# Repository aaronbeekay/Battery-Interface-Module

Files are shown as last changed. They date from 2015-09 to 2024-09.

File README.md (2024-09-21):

Battery Interface Module (BIM)
========================

Battery Interface Module is a compact, 24-cell lithium battery cell monitor with an onboard microcontroller and CAN communications.

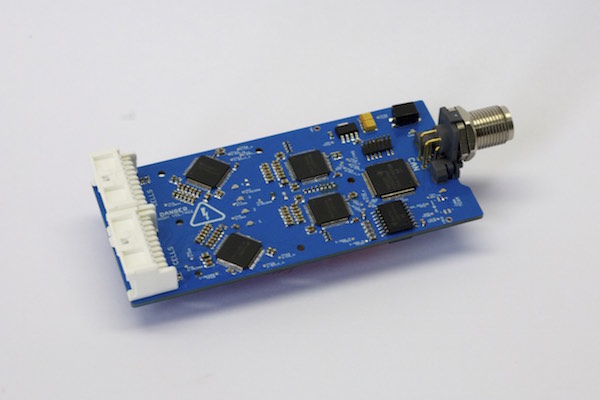
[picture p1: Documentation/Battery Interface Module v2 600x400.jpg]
Image of BIM


*Image: Battery Interface Module v2*

It's built to go on [Buckeye Current](http://current.osu.edu/)'s RW-series electric racing motorcycles. The latest version (v2.0) is designed to integrate with RW-3, a purpose-built racer for the Pikes Peak International Hill Climb.

The Battery Interface Module is built on the TI BQ76PL536A battery-monitor IC. Some features include:

* Voltage monitoring of up to 24 battery cells at precision of ~1 mV
* Thermistor connections for cell temperature monitoring
* Onboard host processor to control battery interface, control balancing, and transmit data over CAN
* Wide input voltage range (4-40 V)
* Isolated interface to battery voltage monitors

You can read more about the Battery Interface Module in the [Battery Interface Module design report]( https://github.com/aaronbeekay/Battery-Interface-Module/raw/main/Documentation/Battery%20Interface%20Module%20report.pdf).

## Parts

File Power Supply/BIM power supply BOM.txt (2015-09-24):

Qty	Description	Mfg Name	Part Num	VID	Vendor Part Num	Parts
4	diode zener 18v 5w axial	ON Semiconductor	1N5355BRLG	DK	1N5355BRLGOSCT-ND	"D1, D2, D3, D4"
1	"2.00mm Pitch MicroClasp? Wire-to-Board Header, Dual Row, Right Angle, 26 Circuits"	Molex	55959-2630	NW	95M2858	X1
2	FUSE BRD MNT 500MA 125VAC 63VDC	Bel Fuse	C1Q 500	DK	507-1075-6-ND	"F1, F2"
20	"Resistor, 1k ohm 63 mW, 1%, 0603"	Multicomp	MC0603WGF1001T5E-TC	NW	58K4448	"R1, R2, R3, R5, R6, R8, R9, R10, R12, R13, R15, R16, R17, R19, R20, R22, R23, R24, R26, R27"
4	"Resistor, 10 ohm, 3W, 5%,"	Multicomp	MOR03SJ0100A19	NW	74M3341	"R7, R14, R21, R28"
4	"CAPACITOR ALUM ELEC, 220UF, 63V, 20%, radial"	Panasonic	ECA-1JM221	NW	96K9194	"C1, C2, C3, C4"
4	*	*	*	*	*	"U$6, U$7, U$8, U$10"
1	"Header, Screw Terminal, 2-pos, 5mm"	TE Connectivity	282836-2	DK	A98076-ND	U$9

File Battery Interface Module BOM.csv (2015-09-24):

Qty | Description | Category | Manufacturer | Manufacturer | Vendor | Vendor part | Cost | Designator
24 | Capacitor, 33 pF, 50V, 5%, NP0, 0402 | Passives | AVX | 04025A330JAT2A | DK | 478-1076-1-ND | 0.02 | C77, C78, C79, C80, C81, C82, C83, C84, C85, C86, C87, C88, C89, C90, C91, C92, C101, C102, C103, C104, C105, C106, C107, C108
1 | DIP switch, 0.05"" pitch, 2pos, 50V | Switches | CTS Electrocomponents | 218-2LPST | DK | CT2182LPST-ND | 1.06 | SW1
1 | M12-5 PCB header, right angle, male pins, shielded | Connectors | Conec | 43-01211 | DK | 626-1513-ND | 10.63 | X4
2 | Micro-Clasp header, 20pos, 2 rows, RA, through-hole | Connectors | Molex | 55959-2030 | NW | 09J7572 | 1.13 | X2, X3
1 | IC, DC/DC Conv, 180MHz, 3.3V-5V in, 3.3V/5V out | ICs | Analog Devices | ADUM5000ARWZ | NW | 19P8235 | 6.99 | IC11
1 | Schottky rectifier, 30V, 1A, SMA | Passives | Diodes Inc | B130-13-F | DK | B130-FDICT-ND | 0.43 | D17
4 | Inductor, Chip, 60ohm, 1.5A, 0603 | Passives | Taiyo Yuden | BKP1608HS600-T | DK | 587-1928-1-ND | 0.047 | L1, L2, L3, L4
4 | IC, Li-Ion battery monitor, LQFP-64 | ICs | Texas Instruments | BQ76PL536APAPT | DK | 296-28926-1-ND | 12.34 | IC1, IC2, IC3, IC4
3 | Capacitor, Ceramic, 470pF 50V, NP0, 0603 | Passives | TDK | C1608C0G1H471J080AA | DK | 445-1289-1-ND | 0.012 | C165, C166, C167
9 | Capacitor, Ceramic, 1UF, 16V, X5R, 10%, 0603 | Passives | TDK | C1608X5R1C105K | NW | 90R7675 | 0.013 | C6, C12, C18, C24, C30, C36, C42, C48, C192
24 | Resistor, 1k ohm, 63 mW, 5%, Thick Film 0402 | CRCW04021K00JNTD | Vishay Dale | CRCW04021K00JNTD | NW | 23C6830 | 0.008 | R10, R11, R12, R47, R48, R49, R50, R51, R52, R53, R54, R55, R56, R57, R58, R59, R60, R61, R62, R63, R64, R65, R66, R67
4 | RES 2.00M OHM 1/16W 1% 0402 SMD | Passives | Vishay Dale | CRCW04022M00FKED | DK | 541-2.00MLCT-ND | 0.005 | R140, R141, R142, R143
12 | Resistor, 1.47k ohm, 100 mW, 0603, 1% | Passives | Vishay Dale | CRCW06031K47FKEA | DK | 541-1.47KHCT-ND | 0.005 | R7, R9, R15, R40, R42, R80, R82, R84, R85, R87, R89, R90
8 | Resistor, 1.82k ohm, 100 mW, 0603, 1% | Passives | Vishay Dale | CRCW06031K82FKEA | DK | 541-1.82KHCT-ND | 0.005 | R6, R8, R39, R41, R81, R83, R86, R88
2 | Resistor, 510k ohm, 100 mW, 1%, Thick Film 0603 | Passives | Vishay Dale | CRCW0603510KFKEA | NW | 52K8595 | 0.005 | R148, R149
1 | Choke, common mode, 100 uH, 500 mA, 25% | Passives | Bourns Inc | DR331-104AE | NW | 29T3649 | 0.32 | L6
25 | Resistor, 1 kohm 100 mW, 1%, Thick Film, 0603 | Passives | Panasonic | ERJ-3EKF1001V | NW | 64R5308 | 0.012 | R1, R2, R3, R4, R5, R13, R14, R16, R17, R18, R20, R21, R22, R23, R24, R26, R27, R28, R29, R30, R32, R33, R34, R35, R36, R135
1 | Resistor, 5.6 kohm, 100 mW, 1%, 0603 | Passives | Panasonic | ERJ-3EKF5601V | NW | 64R5354 | 0.096 | R134
2 | Resistor, 60.4 ohm, 100 mW, 1%, 0603 | Passives | Panasonic | ERJ-3EKF60R4V | NW | 65T8495 | 0.096 | R38, R43
4 | Resistor, 5.5 ohm, 100 mW, 5%, 0603 | Passives | Panasonic | ERJ-3GEYJ5R6V | NW | 65T8659 | 0.002 | R44, R45, R46, R68
2 | Resistor, 82 ohm, 125 mW, 5%, 0805 | Passives | Panasonic | ERJ-6GEYJ820V | NW | 53W4971 | 0.096 | R116, R117
1 | Thermistor, NTC, 10 kohm, 1%, SMD, 0603, b = 3375 K | Passives | Panasonic | ERT-J1VG103FA | NW | 55T6142 | 0.698 | R114
4 | N-channel MOSFET, 25V, 220 mA, SOT-23 | Semiconductors | Fairchild Semiconductor | FDV301N | NW | 58K8856 | 0.034 | Q37, Q39, Q40, Q41
1 | 0.05"" male pin header, 2 rows, 14 positions (TI JTAG) - surface mount, vertical | Connectors | Samtec | FTS-107-01-F-DV | NW | 56P3763 | 0.9 | X6
4 | Capacitor, Ceramic, 10 uF 6.3V, 20%, 0603, X5R | * | Murata | GRM188R60J106ME47D | NW | 24R6334 | 0.12 | C52, C53, C173, C174
18 | Capacitor, Ceramic, 2.2UF, 10%, 25V, 0603, X5R | Passives | Murata | GRM188R61E225KA12D | NW | 13T1193 | 0.107 | C73, C76, C118, C119, C122, C124, C125, C128, C130, C131, C134, C136, C149, C150, C151, C152, C153, C154
57 | Capacitor, Ceramic, 0.1 uF 50V, 10%, 0603, X7R | Passives | Murata | GRM188R71H104KA93D | DK | 490-1519-1-ND | 0.02 | C1, C2, C3, C4, C5, C7, C8, C9, C10, C11, C13, C14, C15, C16, C17, C19, C20, C21, C22, C23, C25, C26, C27, C28, C29, C31, C32, C33, C34, C35, C37, C38, C39, C40, C41, C43, C44, C45, C46, C47, C50, C74, C117, C120, C123, C126, C129, C132, C135, C157, C158, C159, C160, C168, C171, C172, C175
1 | Capacitor, Ceramic, 4.7 nF, 50V, X7R, 10%, 0603 | Passives | Murata | GRM188R71H472KA01D | NW | 38K1673 | 0.006 | C51
2 | Capacitor, Ceramic, 22 uF, 6.3V, X5R, 20%, 0805 | 22 uF | Murata | GRM21BR60J226ME39L | NW | 24R6338 | 0.091 | C190, C191
4 | Capacitor, Ceramic, 10 uF 16V, 10%, X5R, 0805 | Passives | Murata | GRM21BR61C106KE15L | NW | 35R0687 | 0.231 | C75, C121, C127, C133
1 | Capacitor, Ceramic, 1 uF, 50V, X7R, 10%, 1210 | Passives | Murata | GRM32RR71H105KA01L | NW | 97K0677 | 0.248 | C189
4 | LED, Red, 0603, 17mcd | LEDs | Avago | HSMH-C190 | NW | 40K0127 | 0.081 | LED1, LED3, LED4, LED5
1 | IC, Digital Isolator, 150Mbps | ICs | Texas Instruments | ISO7241CDW | NW | 73M3155 | 5.25 | IC9
2 | LED, Green, 0603, 10mcd | LEDs | Osram | LGQ971 | NW | 05M0493 | 0.054 | LED2, LED6
1 | IC, DC-DC Conv, Buck, 42 Vin, 1.25 MHz, SOT23-6 | ICs | Texas Instruments | LMR14206XMKE/NOPB | NW | 76T5004 | 2.72 | IC15
1 | IC, LDO VOLT REG, 3.3V, 0.5A, SOT-223-5 | ICs | Texas Instruments | LP38693MP-3.3/NOPB | NW | 41K7496 | 1.53 | IC6
1 | Diode, Zener, 3 V, 200 mW, SOD-323 | Passives | ON Semiconductor | MM3Z3V0T1G | NW | 09R9502 | 0.017 | D29
24 | Diode, Zener, 5.1V, 200 mW, SOD-323 | Passives | ON Semiconductor | MM3Z5V1T1G | NW | 67H6879 | 0.017 | D3, D4, D5, D6, D7, D8, D9, D10, D11, D12, D13, D14, D15, D16, D19, D20, D21, D22, D23, D24, D25, D26, D27, D28
4 | RES 510K OHM 1/16W 1% 0402 SMD | Passives | Yageo | RC0402FR-07510KL | DK | 311-510KLRCT-ND | 0.011 | R144, R145, R146, R147
4 | Resistor, 100 ohm, 62.5 mW, 1%, 0402 | Passives | Yageo | RC0402FR-13100RL | NW | 67R9962 | 0.007 | R126, R128, R130, R132
1 | Resistor, 36 kohm, 1%, 100 mW, 0603 | Passives | Yageo | RC0603FR-0736KL | DK | 311-36.0KHRCT-ND | 0.0108 | R136
7 | Resistor, 10k ohm 100 mW, 5%, 100ppm, 0603 | Passives | Yageo | RC0603JR-1010KL | NW | 68R0215 | 0.008 | R137, R138, R139, R154, R155, R157, R158, R161
1 | Inductor, 18 uH, 1.5 A, unshielded, 15%, 8012 | Passives | Bourns | SDR0604-180YL | DK | SDR0604-180YLCT-ND | 0.47 | L5
2 | TVS DIODE 30VWM 48.4VC SMB | Passives | Littelfuse | SMBJ30CA | DK | SMBJ30CALFCT-ND | 0.423 | D1, D2
1 | IC, CAN TX/RX, 1 MBps, 5.5V, 8-SOIC | ICs | Texas Instruments | SN65HVD1050D | NW | 70K4439 | 1.32 | IC8
1 | IC, Buffer, 2-bit, non-invert, open drain, SOT-23-6 | ICs | Texas Instruments | SN74LVC2G07DBVR | DK | 296-13494-1-ND | 0.59 | IC14
1 | Diode, Schottky, 40V, 500 mA, SOD-123 | Passives | STMICROELECTRONICS | STPS0560Z | NW | 89K1573 | 0.762 | D18
2 | Capacitor, Tantalum, 100 uF, 6.3V, 10%, 1411 | Passives | AVX | TAJB107K006RNJ | NW | 60R5877 | 0.633 | C49, C54
1 | IC, MCU, C2000 piccolo, LQFP80 | ICs | Texas Instruments | TMS320F28035PNT | DK | 296-32764-ND | 12.38 | IC7

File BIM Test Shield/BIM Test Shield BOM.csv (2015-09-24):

Qty | Description | Category | Manufacturer | Manufacturer | Vendor | Vendor part | Cost | Designator
33 | Pin, Spring Loaded, pogo. 7.5mm max height x 1.4mm stroke | Connector | Mill-Max | 0908-2-15-20-75-14-11-0 | DK | ED90386-ND | 0.6972
33 | Miniature test point, white, 0.04" dia. Mounting hole | Connector | Keystone | 5002 | DK | 5002K-ND | 0.327

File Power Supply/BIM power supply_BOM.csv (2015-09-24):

Qty | Description | Category | Manufacturer | Mfg part | Vendor | Vendor Part | Unit Cost | Designator
4 | diode zener 18v 5w axial | Diode | ON Semiconductor | 1N5355BRLG | DK | 1N5355BRLGOSCT-ND | 0.54 | D1, D2, D3, D4
1 | 2.00mm Pitch MicroClasp? Wire-to-Board Header, Dual Row, Right Angle, 26 Circuits | Connector* | Molex | 55959-2630 | NW | 95M2858 | 1.16 | X1
2 | FUSE BRD MNT 500MA 125VAC 63VDC | Fuse | Bel Fuse | C1Q 500 | DK | 507-1075-6-ND | 0.31 | F1, F2
20 | Resistor, 1k ohm 63 mW, 1%, 0603 | Resistor | Multicomp | MC0603WGF1001T5E-TC | NW | 58K4448 | 0.06 | R1, R2, R3, R5, R6, R8, R9, R10, R12, R13, R15, R16, R17, R19, R20, R22, R23, R24, R26, R27
4 | Resistor, 10 ohm, 3W, 5%, | Resistor | Multicomp | MOR03SJ0100A19 | NW | 74M3341 | 0.09 | R7, R14, R21, R28
4 | CAPACITOR ALUM ELEC, 220UF, 63V, 20%, radial | Capacitor | Panasonic | ECA-1JM221 | NW | 96K9194 | 0.5 | C1, C2, C3, C4
4 | Trimpot, 10K, vertical | Pot | Bourns Inc | 3362P-1-103LF | DK | 3362P-103LF-ND | 1.02 | U$6, U$7, U$8, U$10
1 | Header, Screw Terminal, 2-pos, 5mm | Connector | TE Connectivity | 282836-2 | DK | A98076-ND | 0.9 | U$9

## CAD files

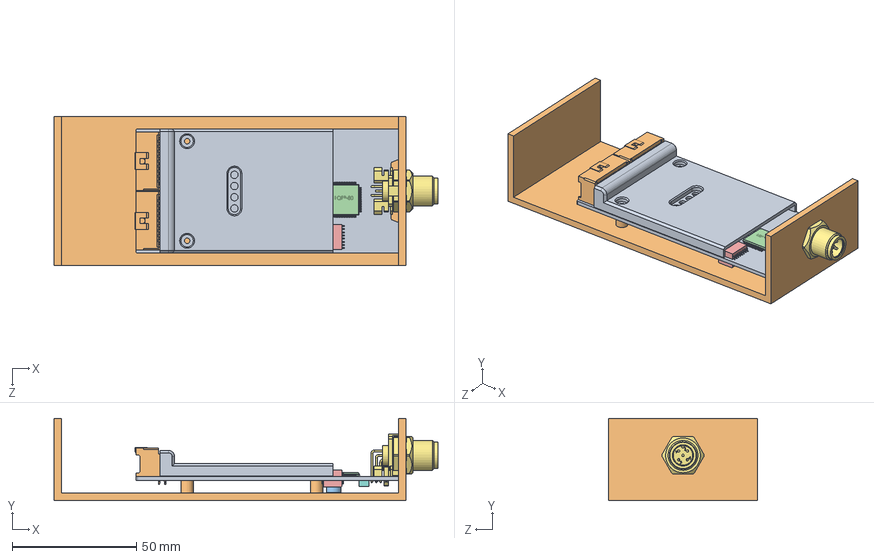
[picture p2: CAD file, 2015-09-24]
MCAD/BIM.SLDASM
154.3 x 33.0 x 60.0 mm
BIM PCB
Micro-Clasp 20ckt dual-row header - 55959-2030 x 2
SDR0604
User Library-LQFP-80
User Library-SOIC-16-1 x 2
User Library-LQFP64-1-1 x 4
M12_5pos_RA_header
DO-214AA^BIM x 2
BIM cover^BIM
BIM mount

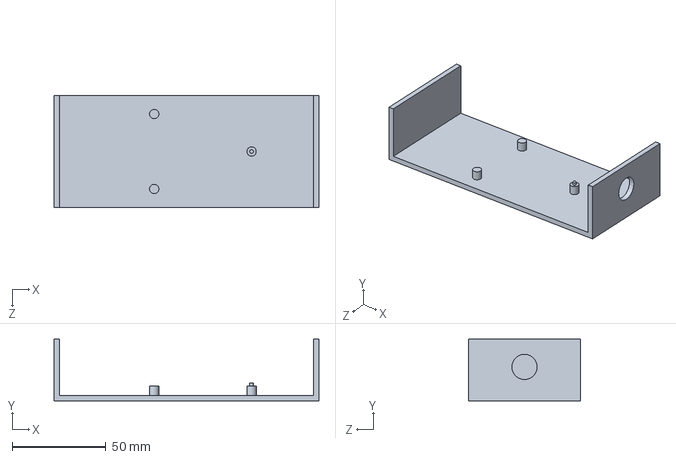
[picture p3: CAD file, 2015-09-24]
MCAD/BIM mount.SLDPRT
141.5 x 33.0 x 60.0 mm

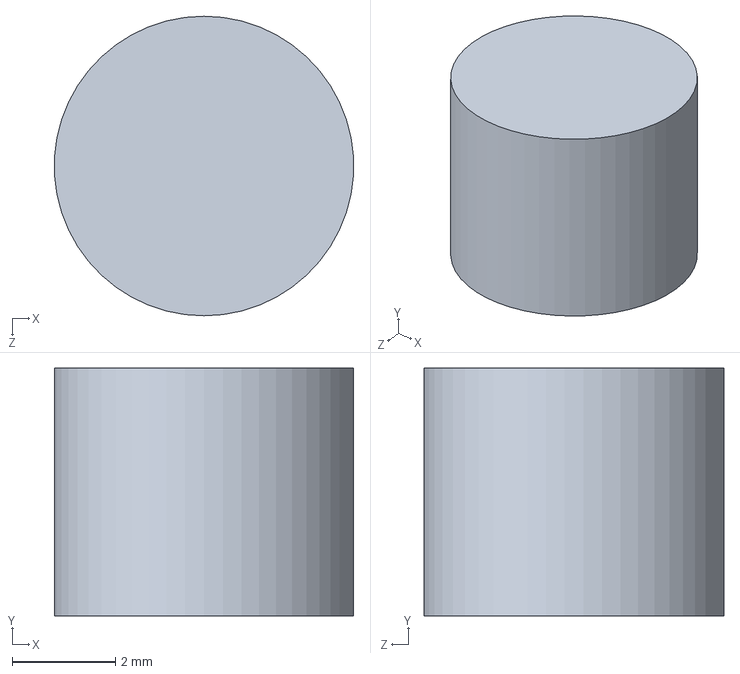
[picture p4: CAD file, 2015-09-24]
MCAD/SDR0604.SLDPRT
5.79 x 4.80 x 5.80 mm

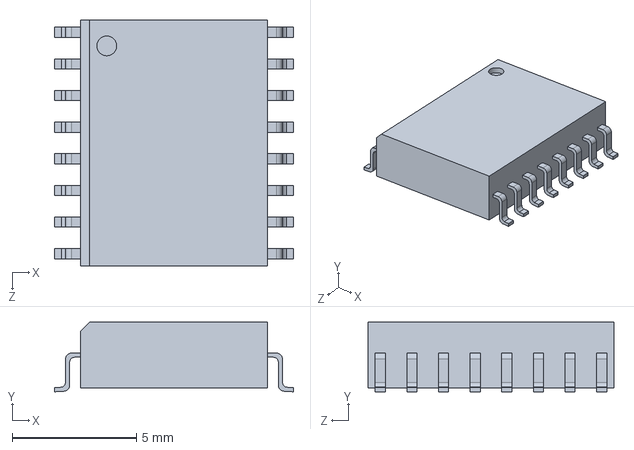
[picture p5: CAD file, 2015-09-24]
MCAD/User Library-SOIC-16-1.SLDPRT
9.60 x 2.80 x 9.90 mm

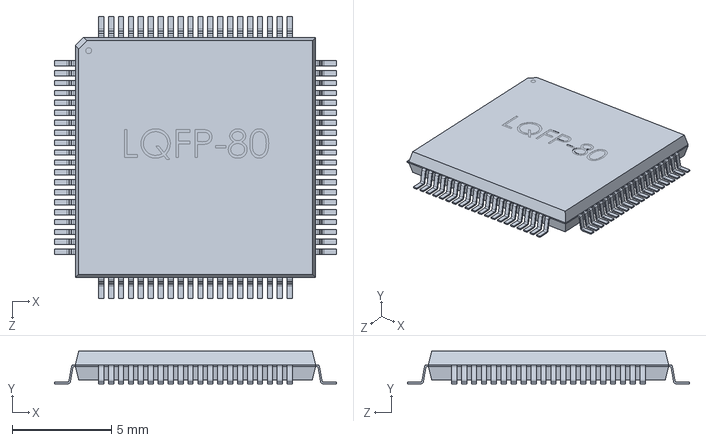
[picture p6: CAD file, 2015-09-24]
MCAD/User Library-LQFP-80.SLDPRT
14.2 x 1.64 x 14.2 mm

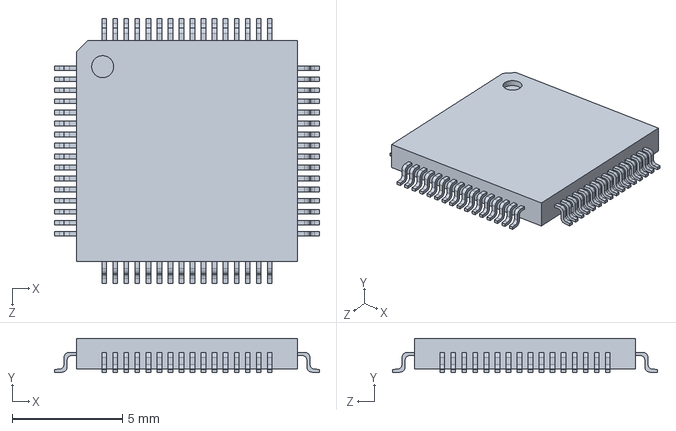
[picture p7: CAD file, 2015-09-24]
MCAD/User Library-LQFP64-1-1.SLDPRT
12.0 x 1.56 x 12.0 mm

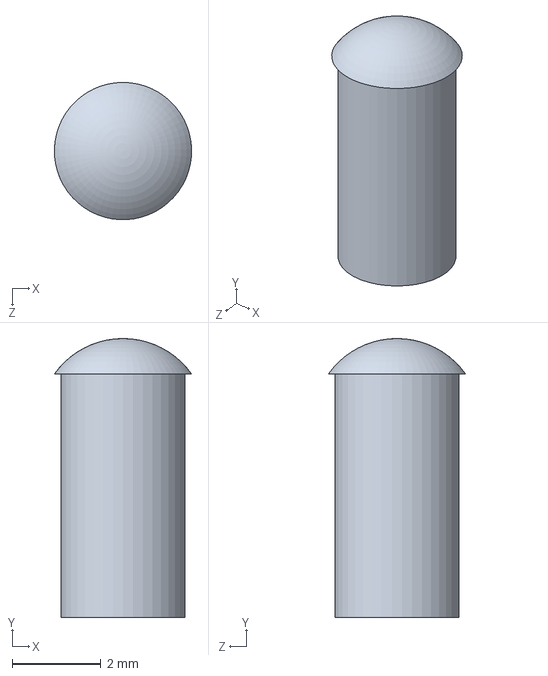
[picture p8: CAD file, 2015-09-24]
MCAD/Bivar PLP2-XXX light pipe.SLDPRT
3.10 x 6.30 x 3.10 mm

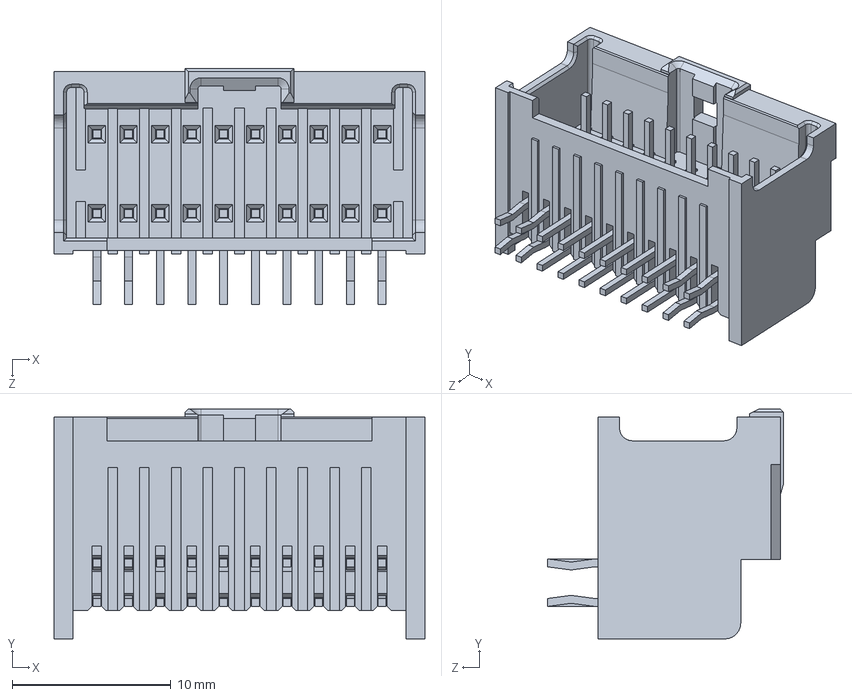
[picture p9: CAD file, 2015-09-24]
MCAD/Micro-Clasp 20ckt dual-row header - 55959-2030.SLDPRT
23.4 x 14.5 x 14.9 mm

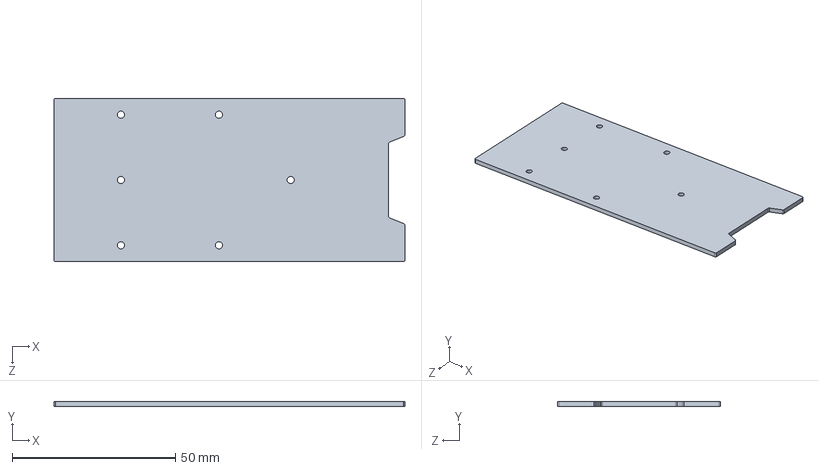
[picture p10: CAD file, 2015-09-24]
MCAD/BIM PCB.SLDPRT
107.5 x 1.60 x 50.0 mm

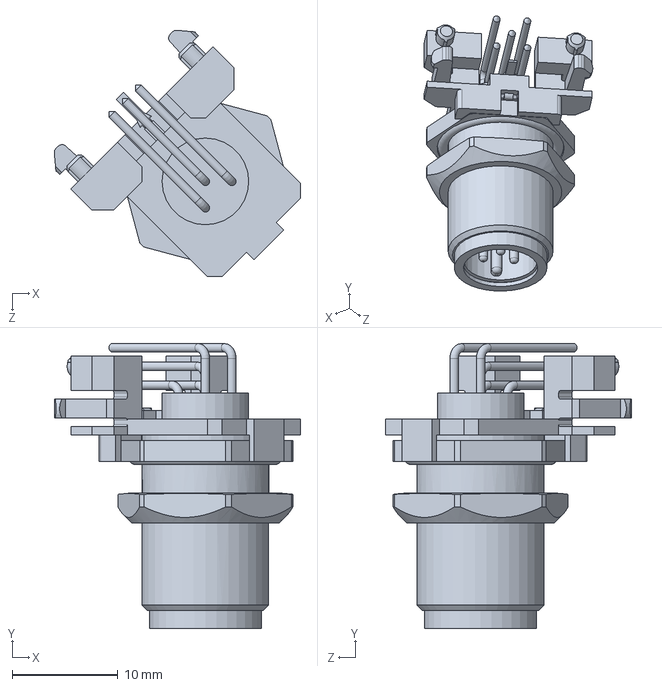
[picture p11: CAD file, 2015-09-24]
MCAD/M12_5pos_RA_header.SLDPRT
23.3 x 27.0 x 23.3 mm

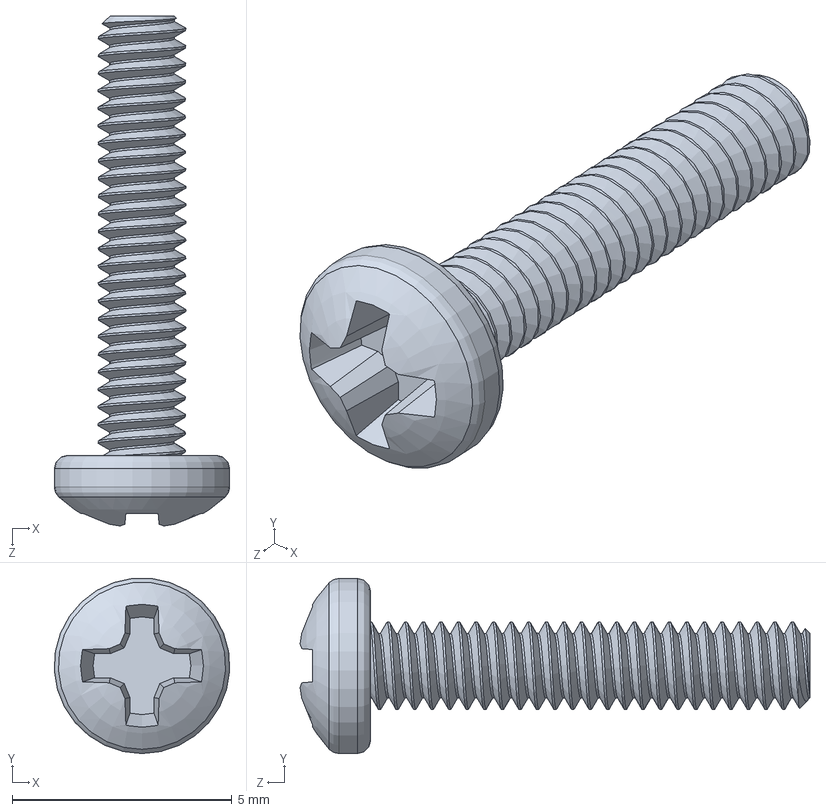
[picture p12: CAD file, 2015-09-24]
MCAD/90116A020.SLDPRT
3.99 x 3.99 x 11.6 mm

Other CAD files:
MCAD/BIM.SLDDRW

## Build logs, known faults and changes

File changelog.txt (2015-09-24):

Changelog - Battery Interface Module

# v1.0.0 (r01)
Initial version.

# v1.0.1 (r02)
Bugfixes.

# v2.0.0
BIM v2 is a redesign for RW-3.

## Major changes
* Redesign to be a 24-cell monitor (not 36).
* Remove onboard balancing circuit.
* Remove CAN auto-termination circuit and replace with termination switch.
* Updated CAN communications circuit for improved robustness to electromagnetic noise.
* Reduce size and height to integrate with RW-3 battery pack.

## Detailed changelog
* Update per-cell filter circuit to improve performance.
* Remove one digital isolator -- no longer pass CONV, DRDY, FAULT, ALERT to host processor.
* Update CAN circuit to use ISO1050 and add common-mode choke.
* Change CAN/power connector to M12 circular connector.
* Reduce power loss capacitance from 1000 uF to 200 uF.
* Include series resistance in VBAT lines to '536A ICs in order to mitigate hot-plug inrush current device destruction issue.
* Include per-cell Zener diodes before low-pass filter.
* New form factor and mounting.
* Added pogo-pin test points to improve debugging accessibility.
* Call out commonly modified components (stack communication components, stack termination components) on silkscreen layer for convenience.
* Reduce use of 0402-size components and eliminate 0402-size resistor arrays for reliability when hand soldered.
* Remove CAN auto-termination circuit, add switch to terminate CAN.
* Add "CAN-TX" LED. Remove one CPU-controlled LED.
* Remove both pushbuttons.
* Remove both pushbutton indicator lights.
* JTAG header is now 0.05" pitch.
* Add separate +5V rail to power SN65HVD1050 (CAN transceiver).

#v2.0.1
* Increase test point text size for legibility.

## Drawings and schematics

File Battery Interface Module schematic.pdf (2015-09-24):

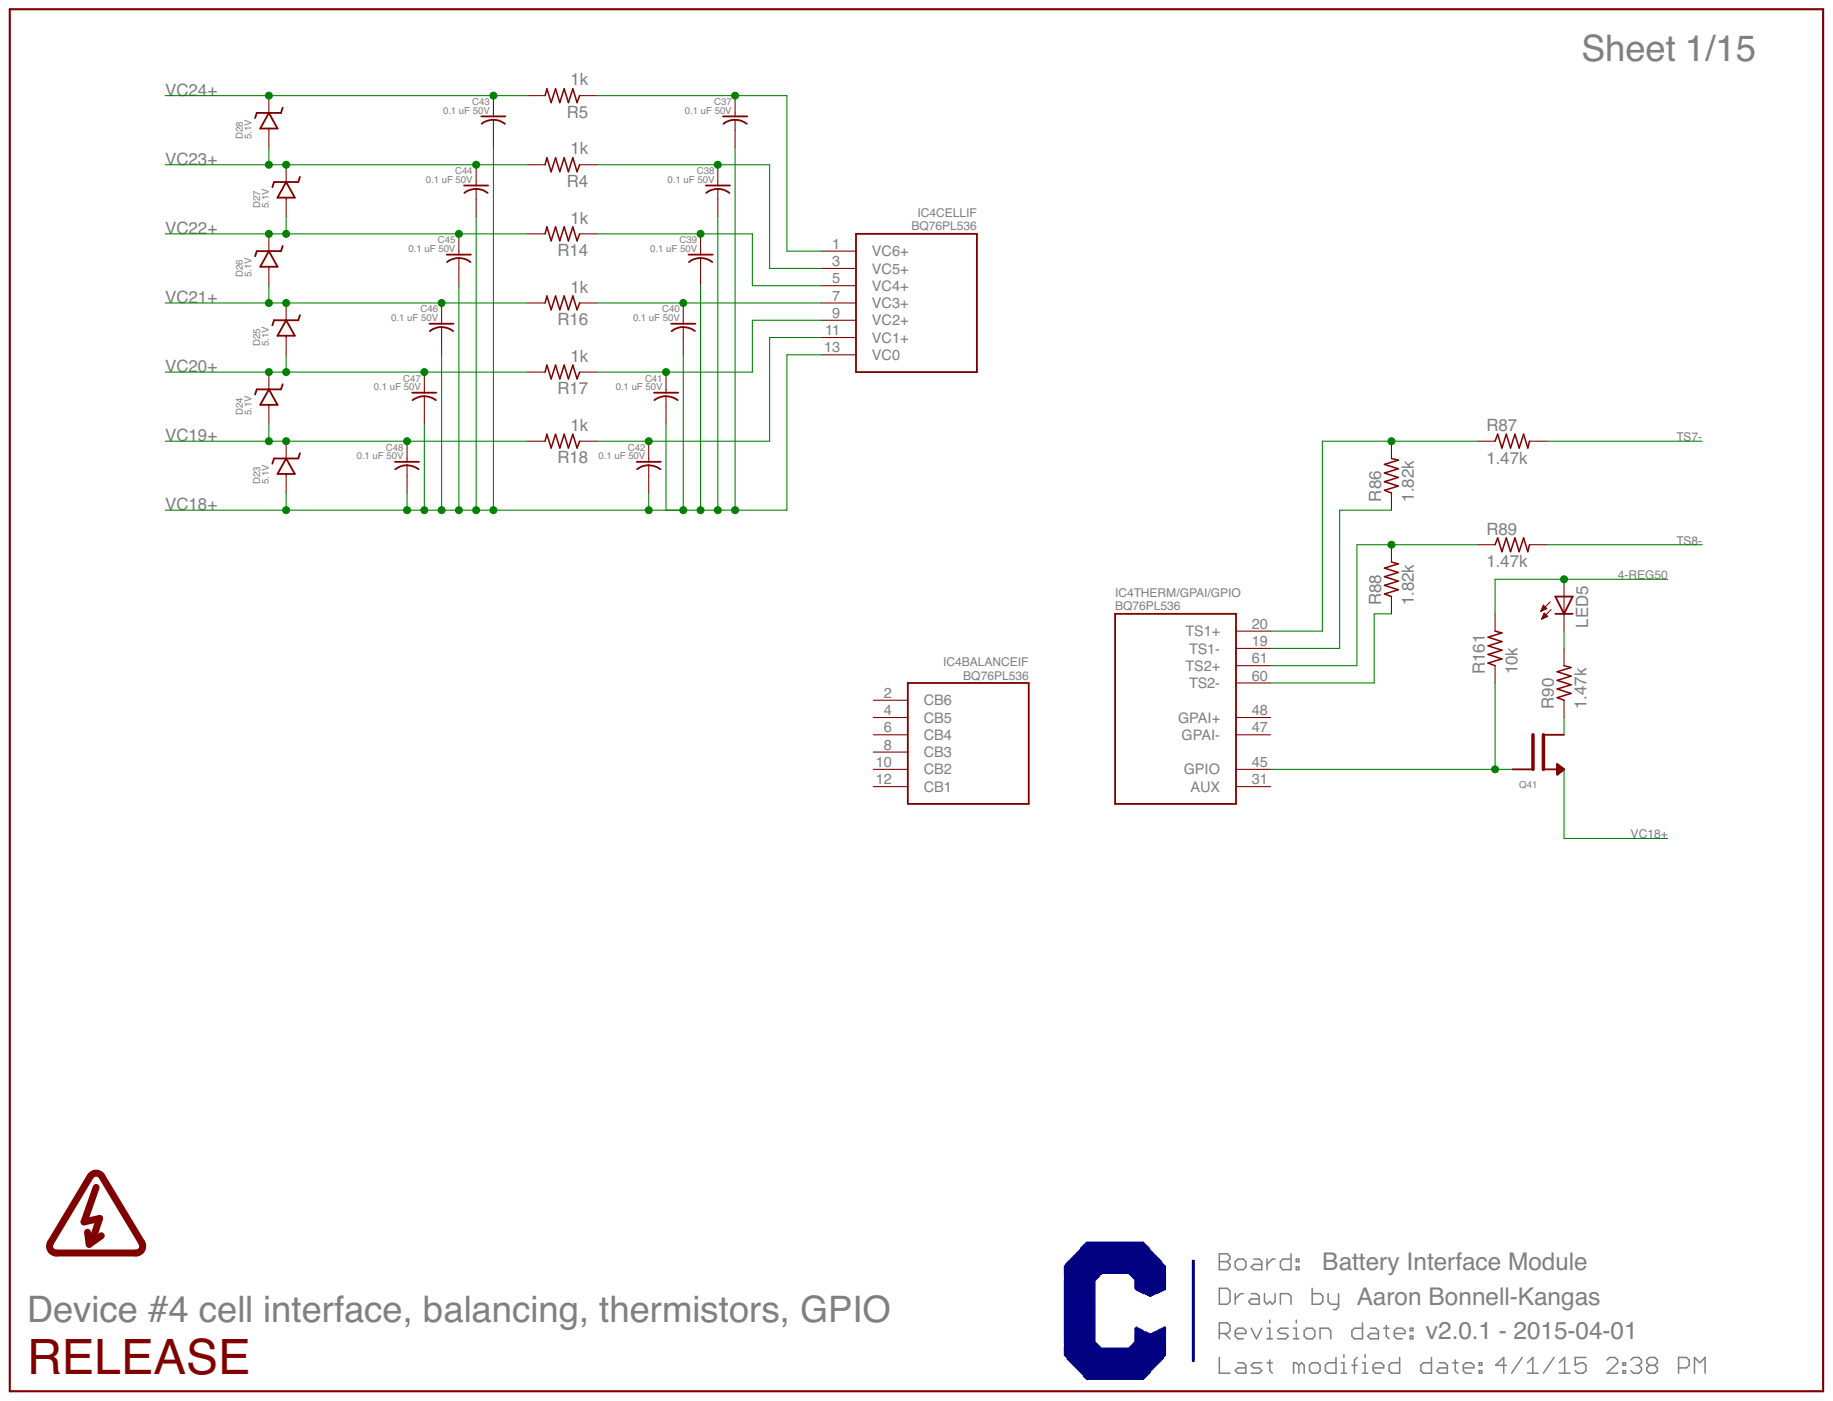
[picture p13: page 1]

Device #4 cell interface, balancing, thermistors, GPIO
RELEASE

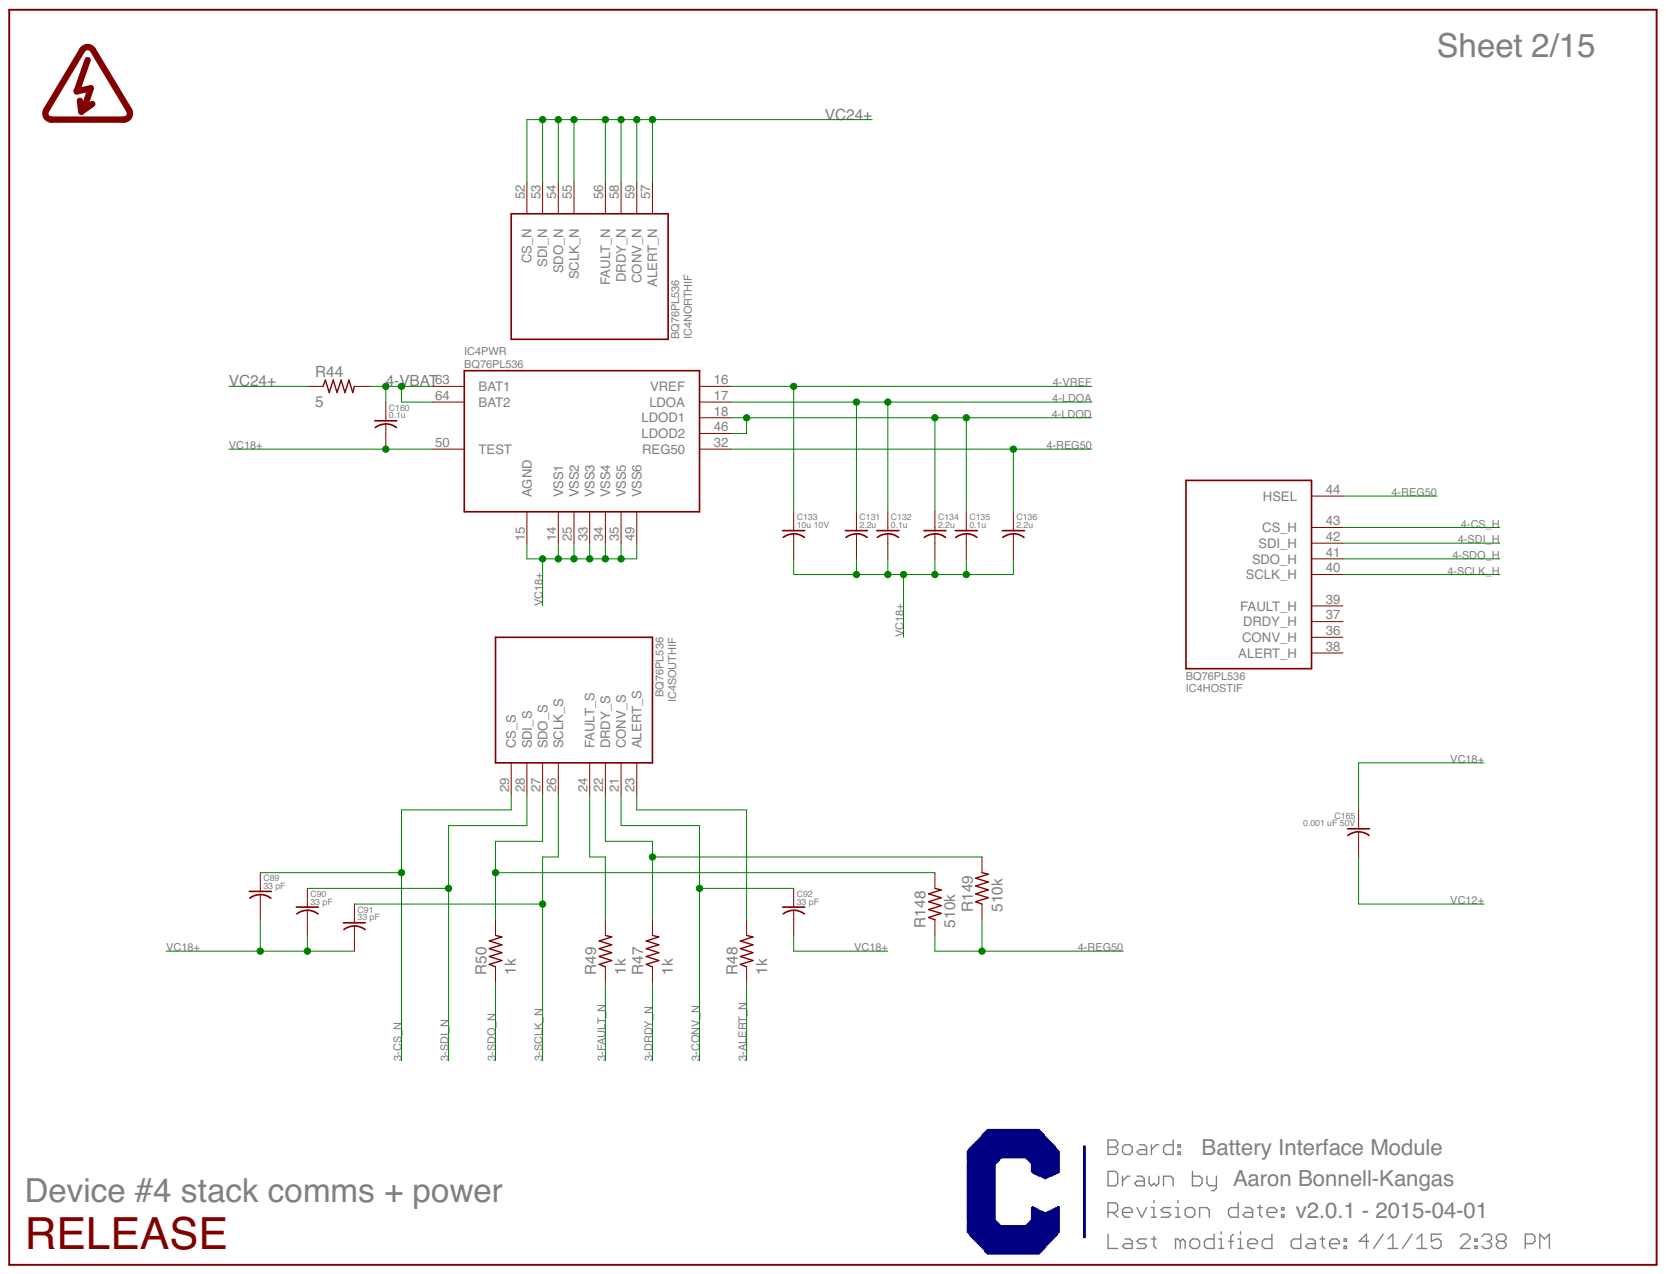
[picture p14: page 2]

Device #4 stack comms + power

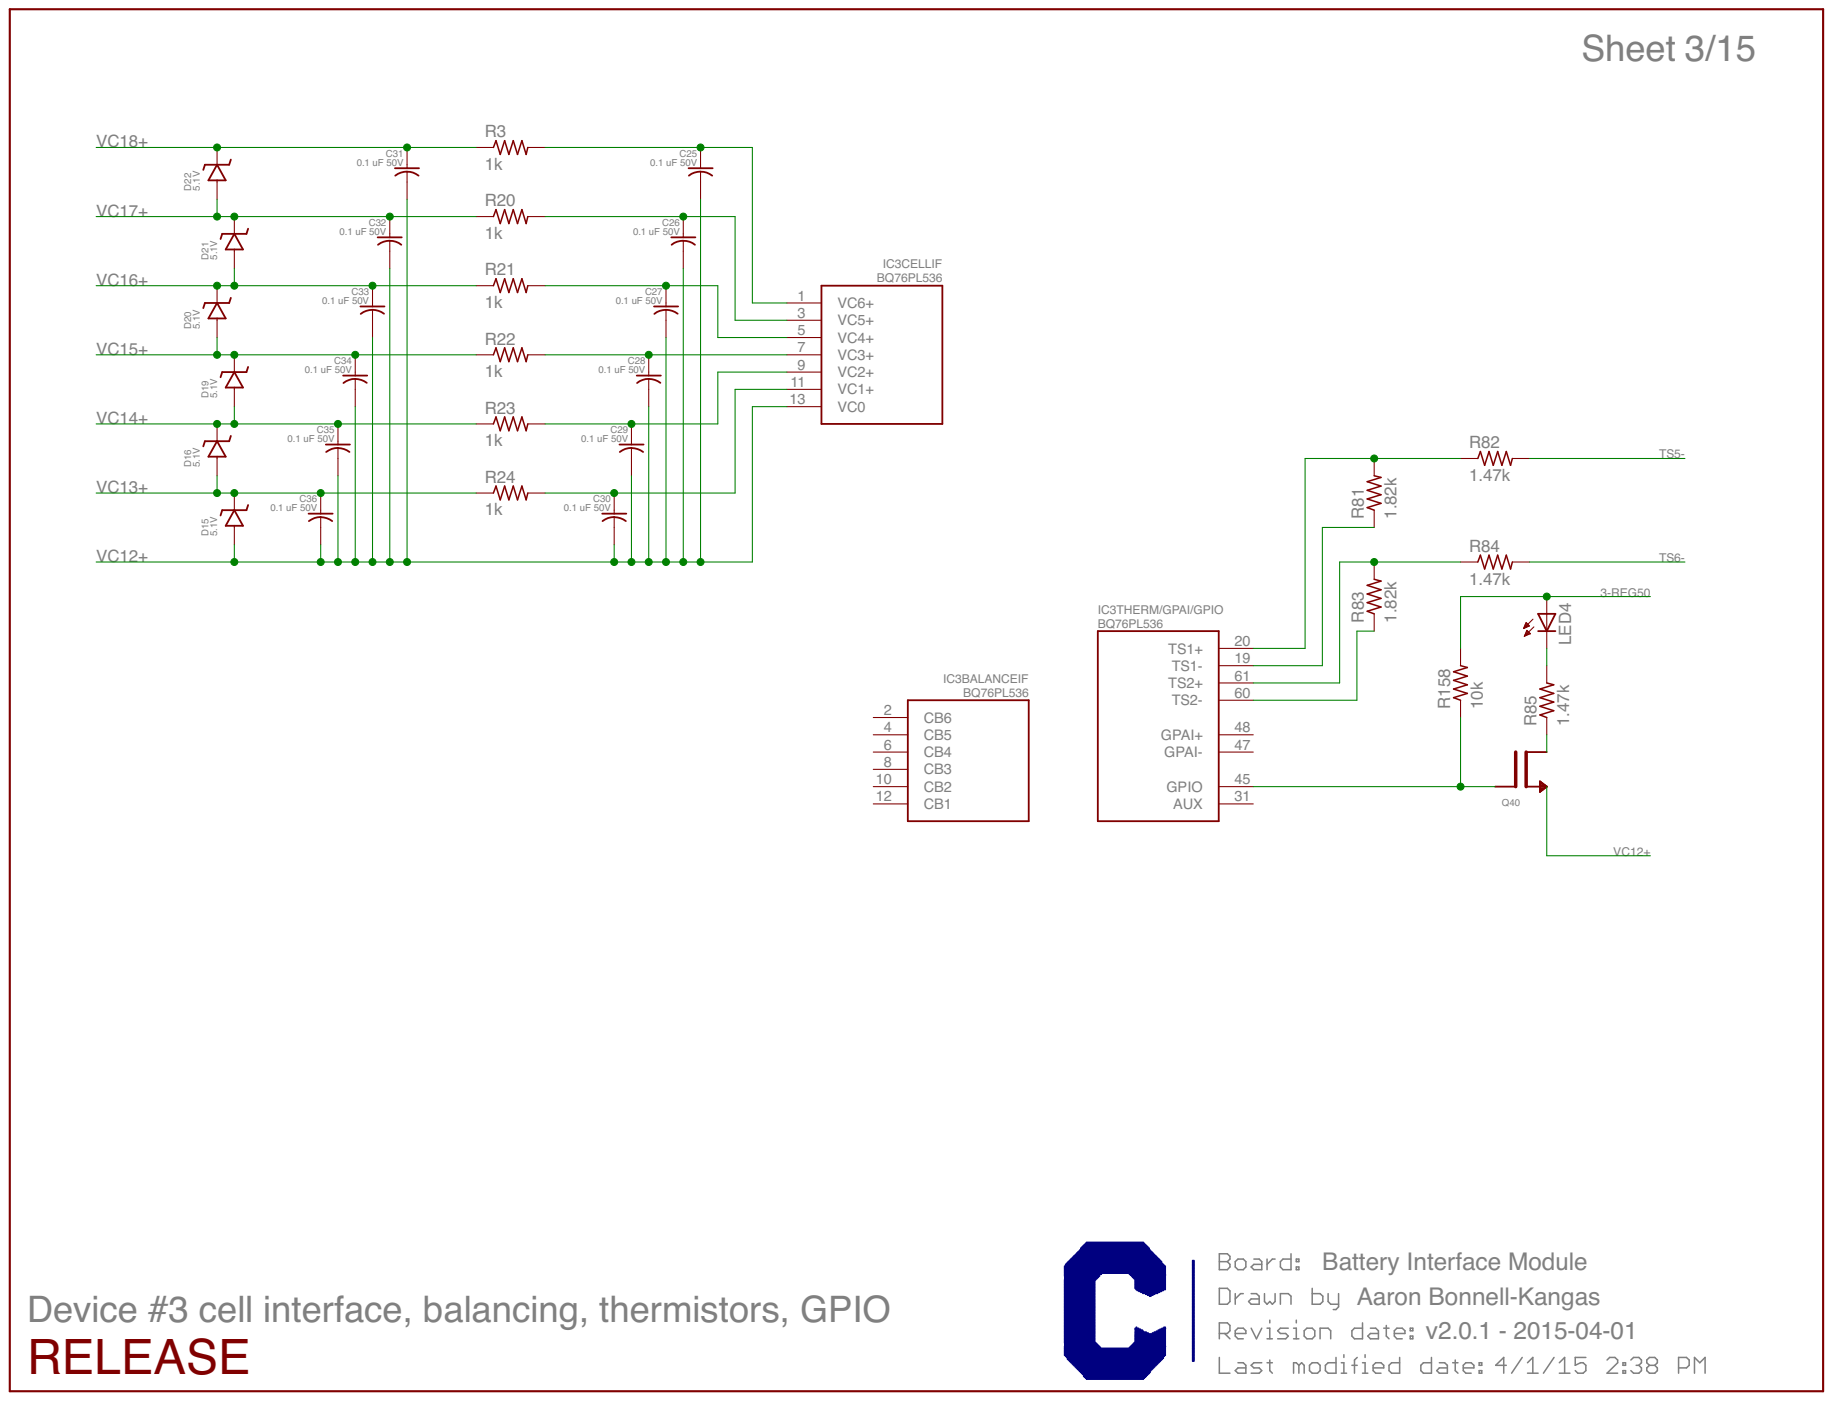
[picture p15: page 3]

Device #3 cell interface, balancing, thermistors, GPIO

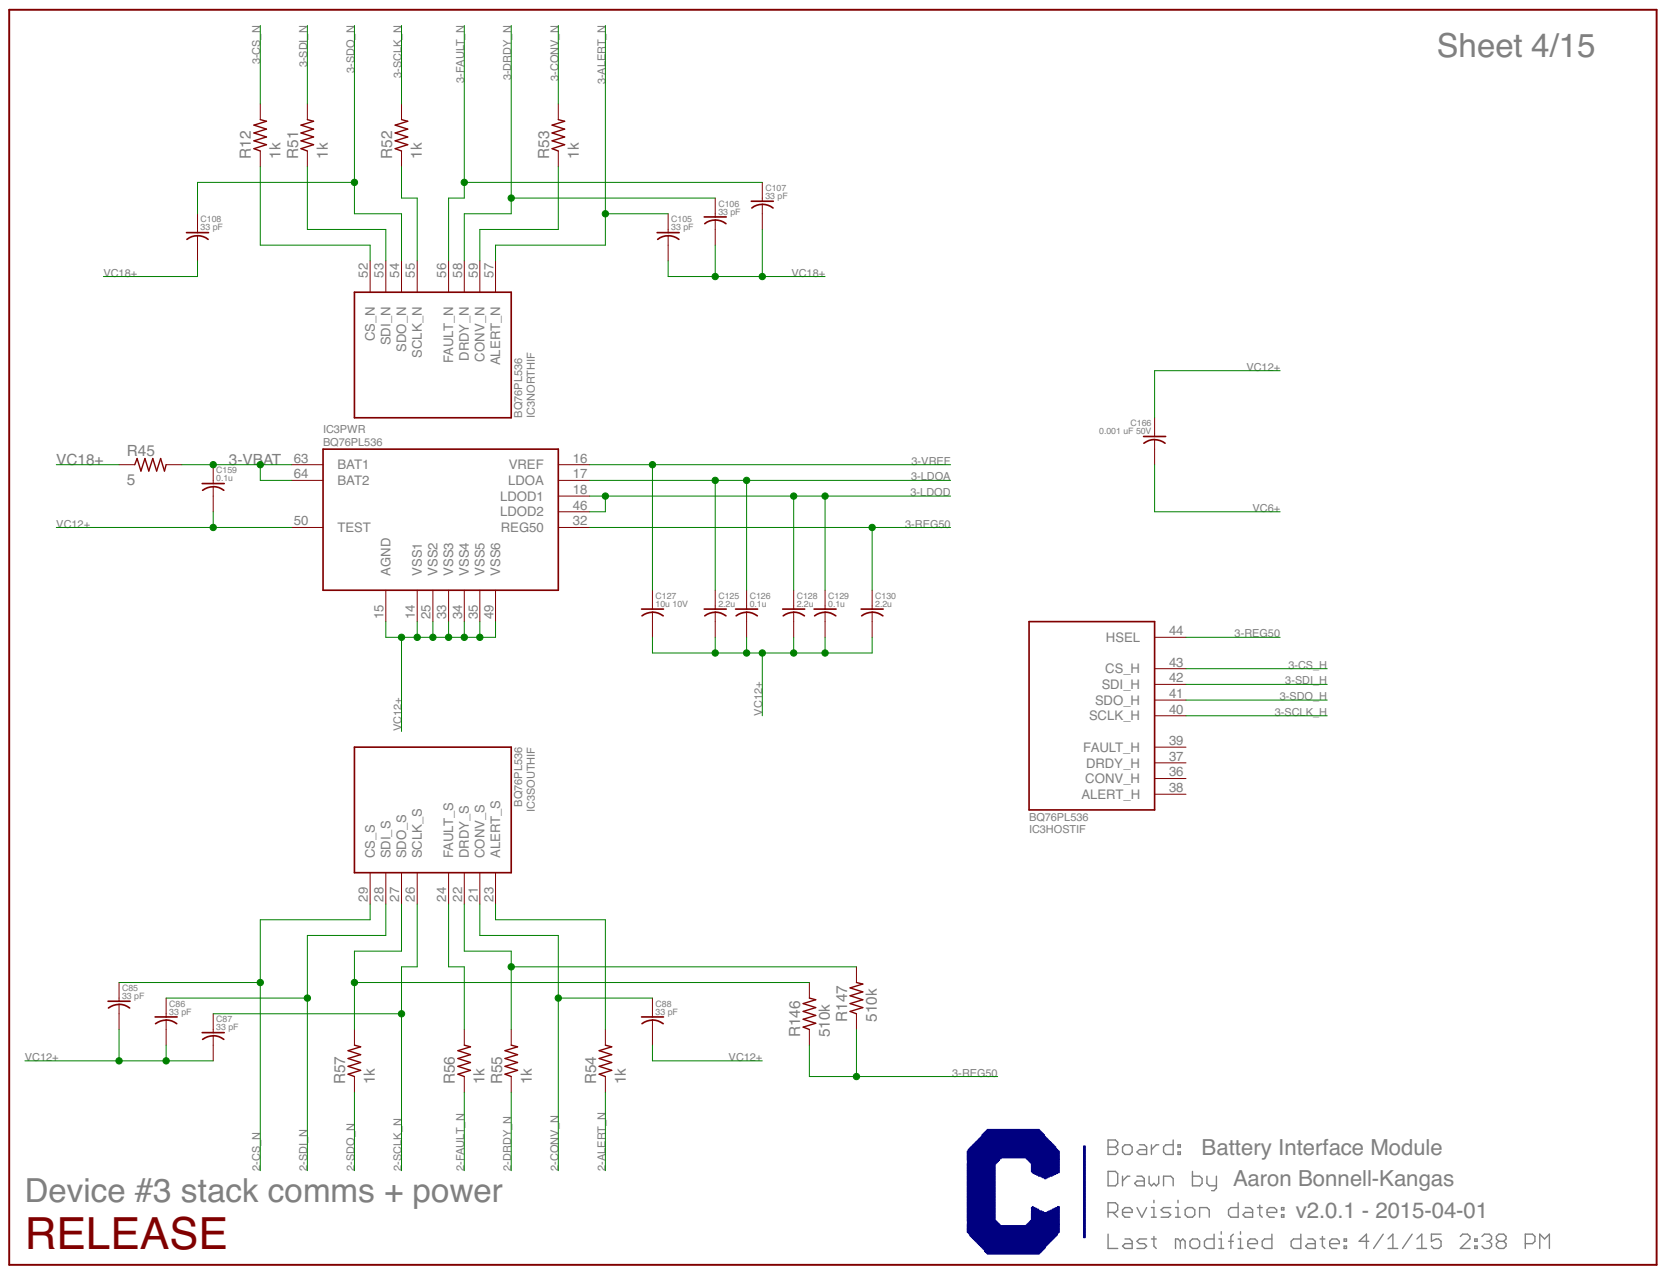
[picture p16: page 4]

Device #3 stack comms + power

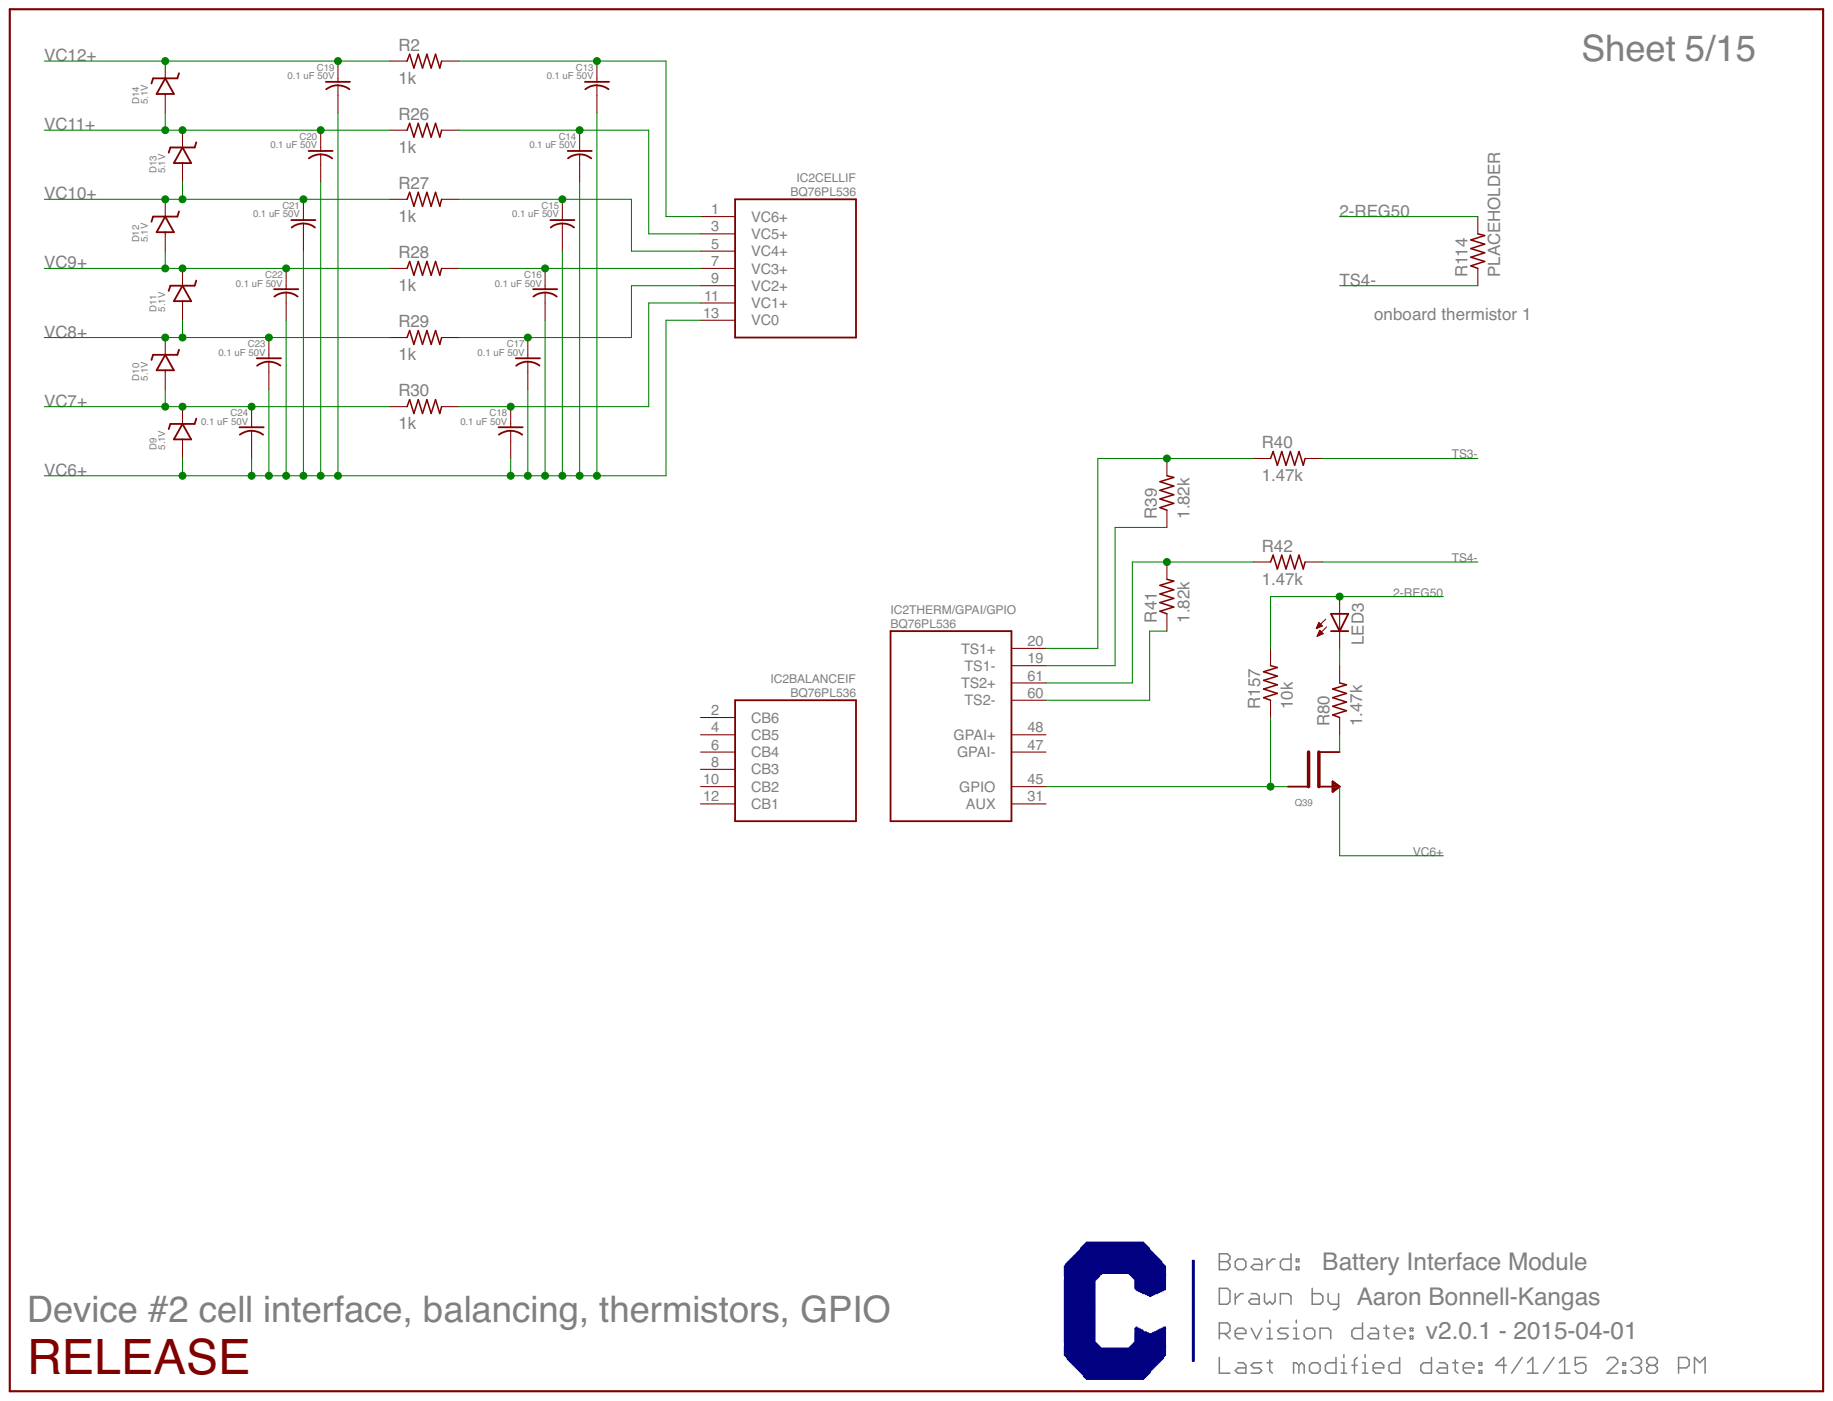
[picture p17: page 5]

Device #2 cell interface, balancing, thermistors, GPIO

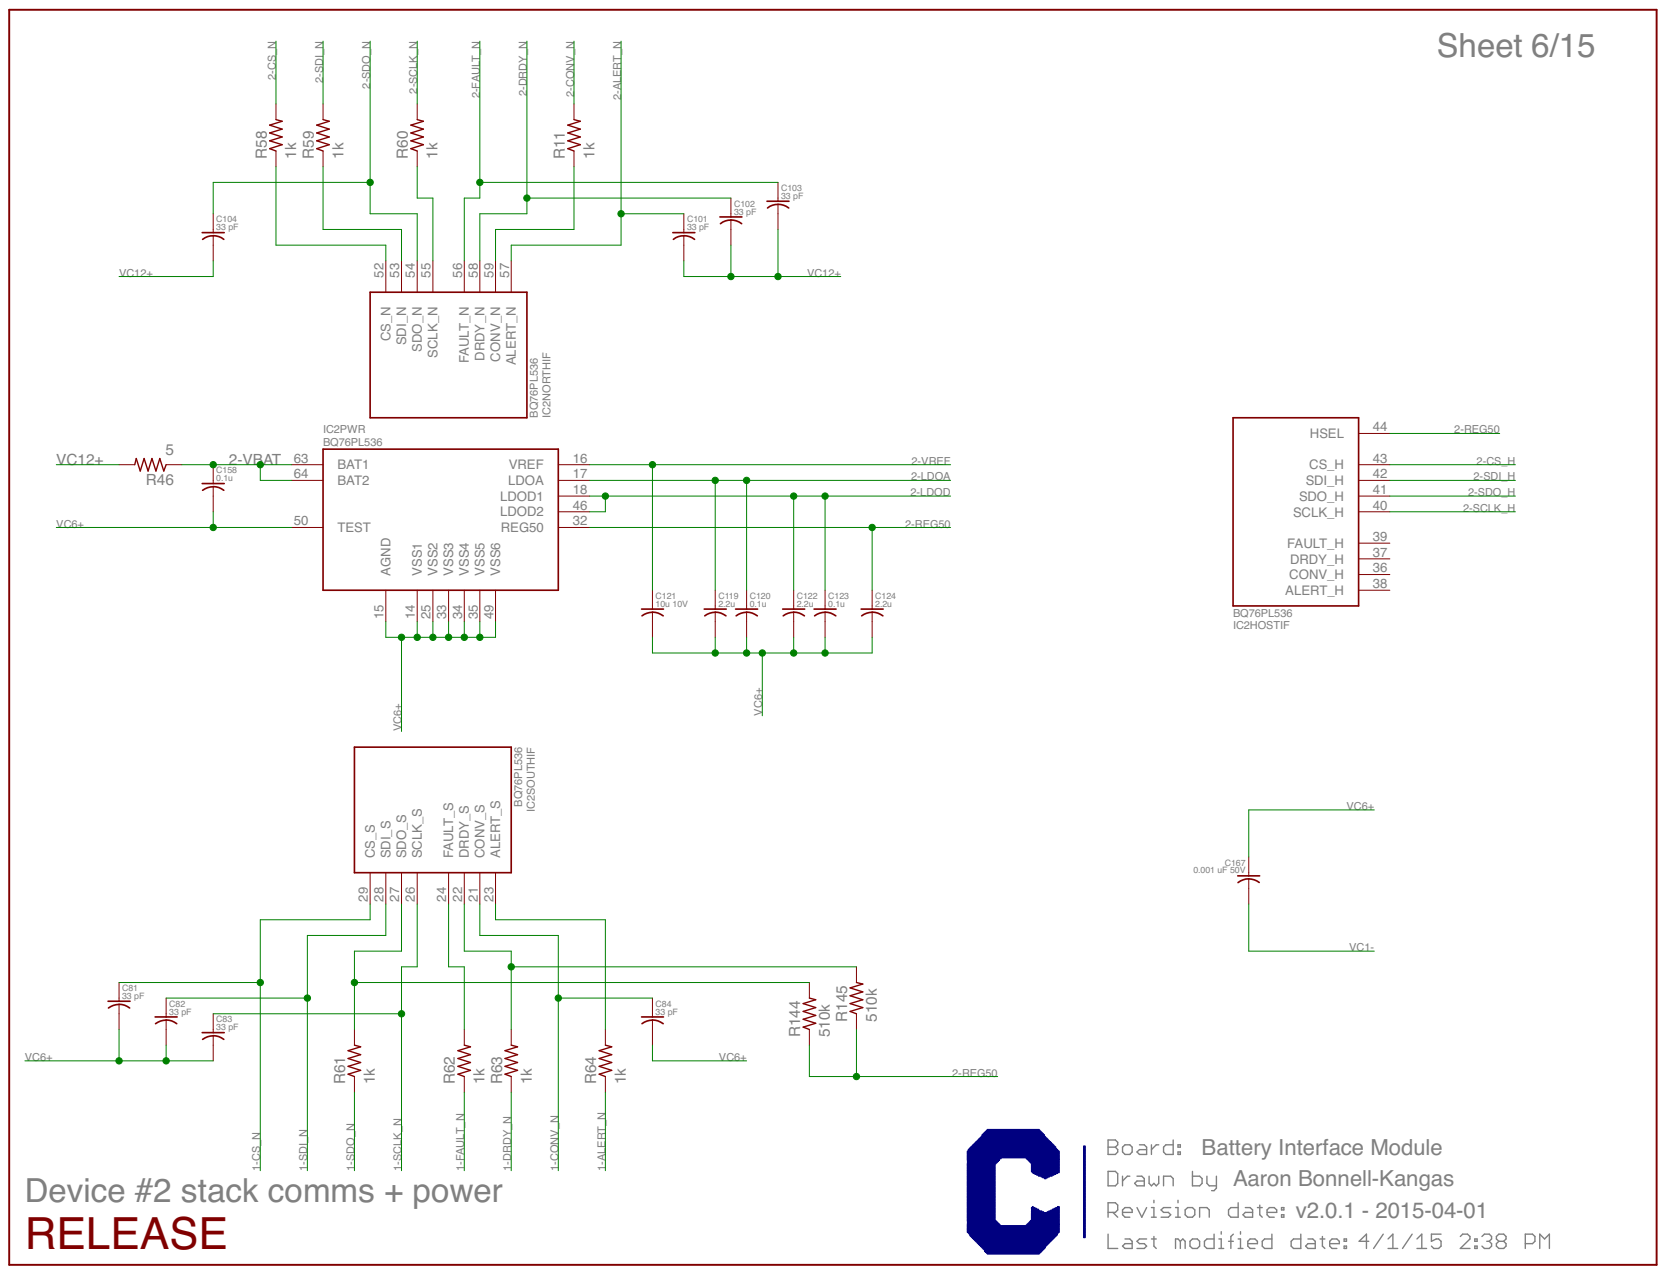
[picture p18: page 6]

Device #2 stack comms + power

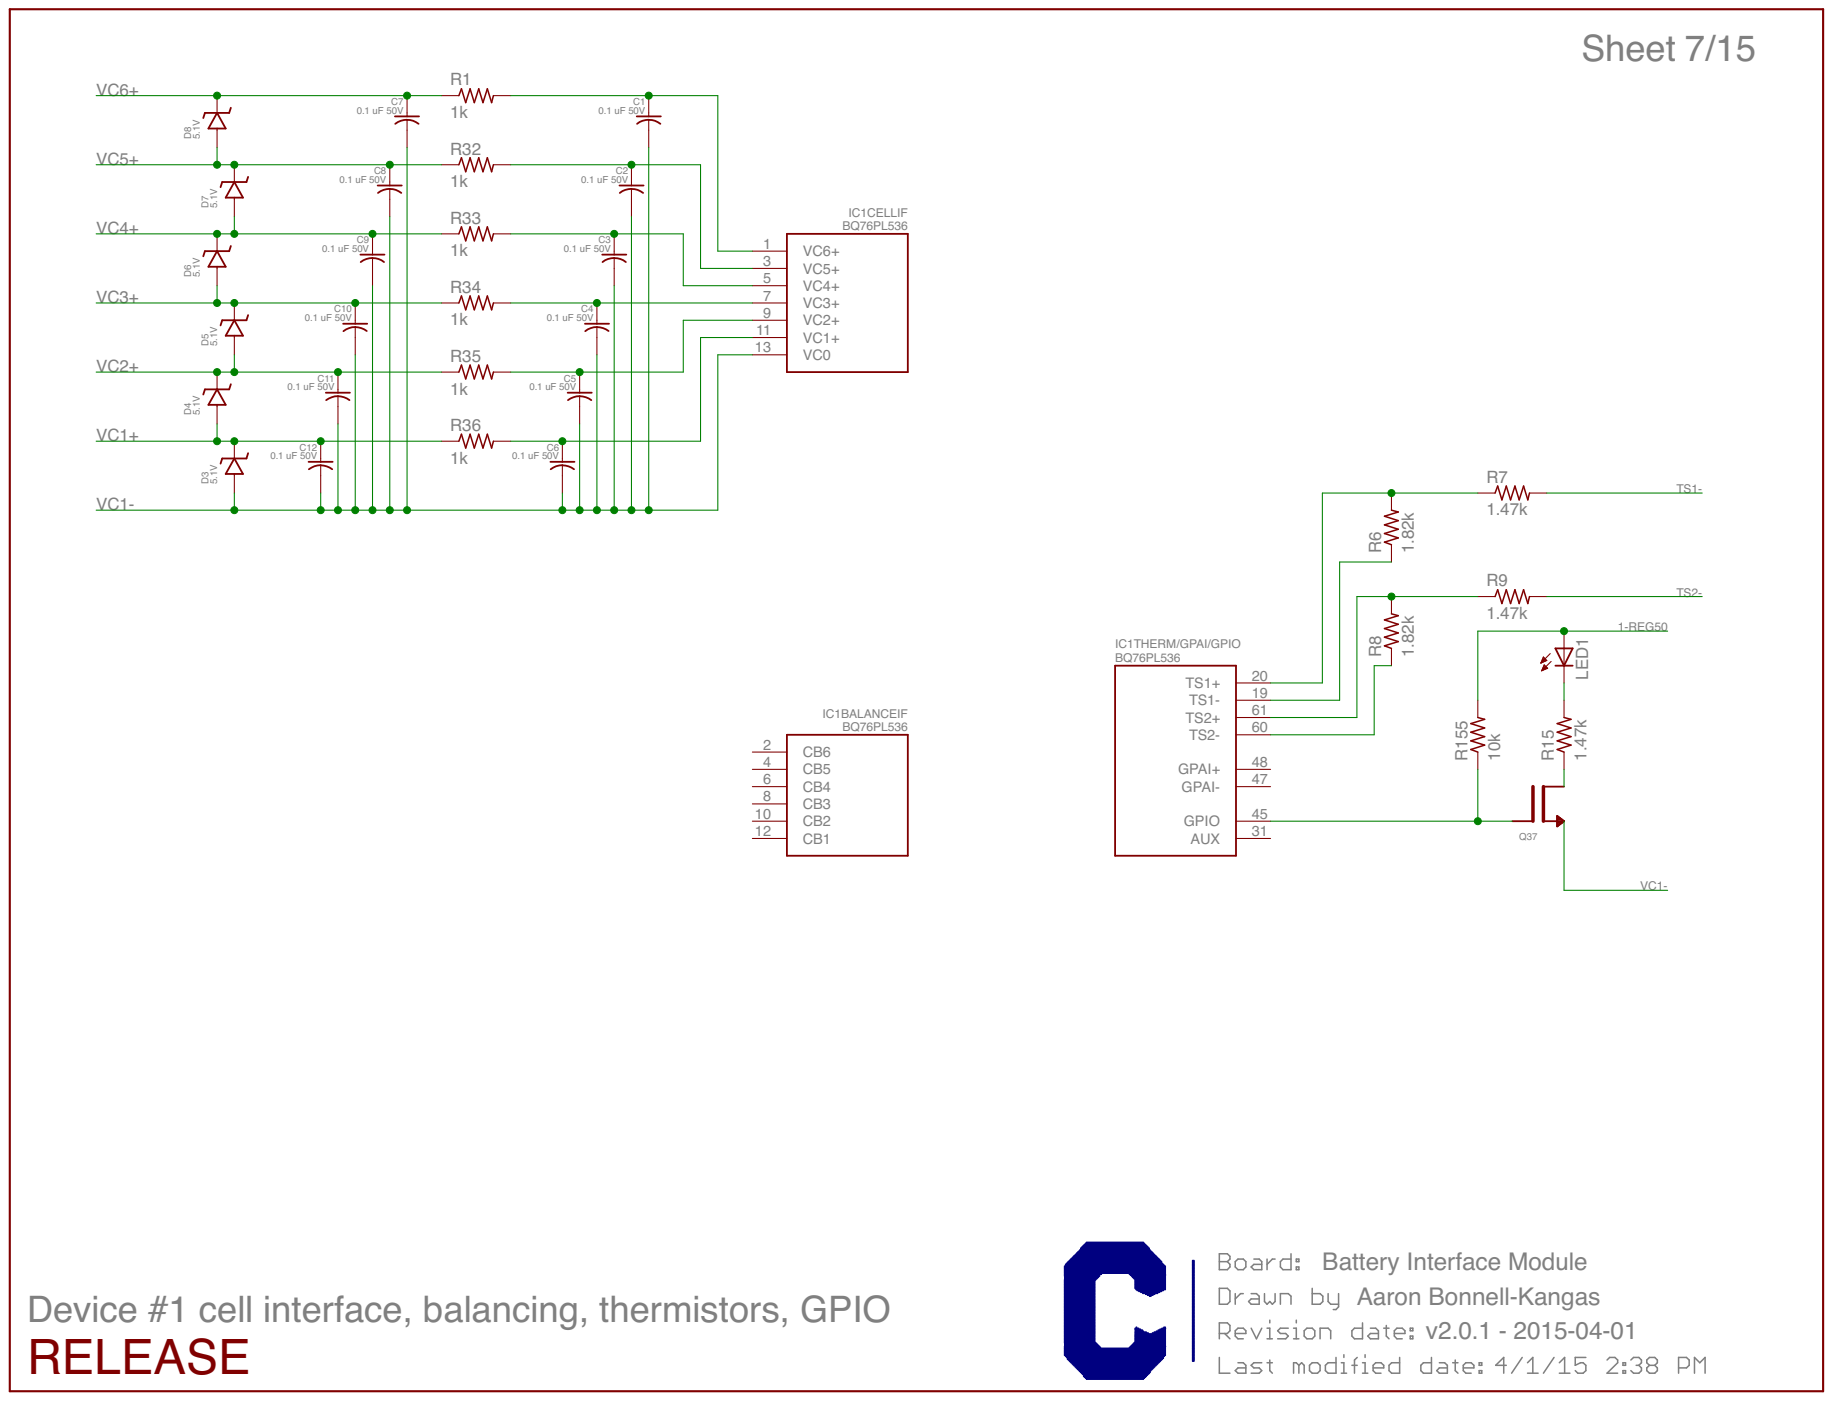
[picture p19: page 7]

Device #1 cell interface, balancing, thermistors, GPIO

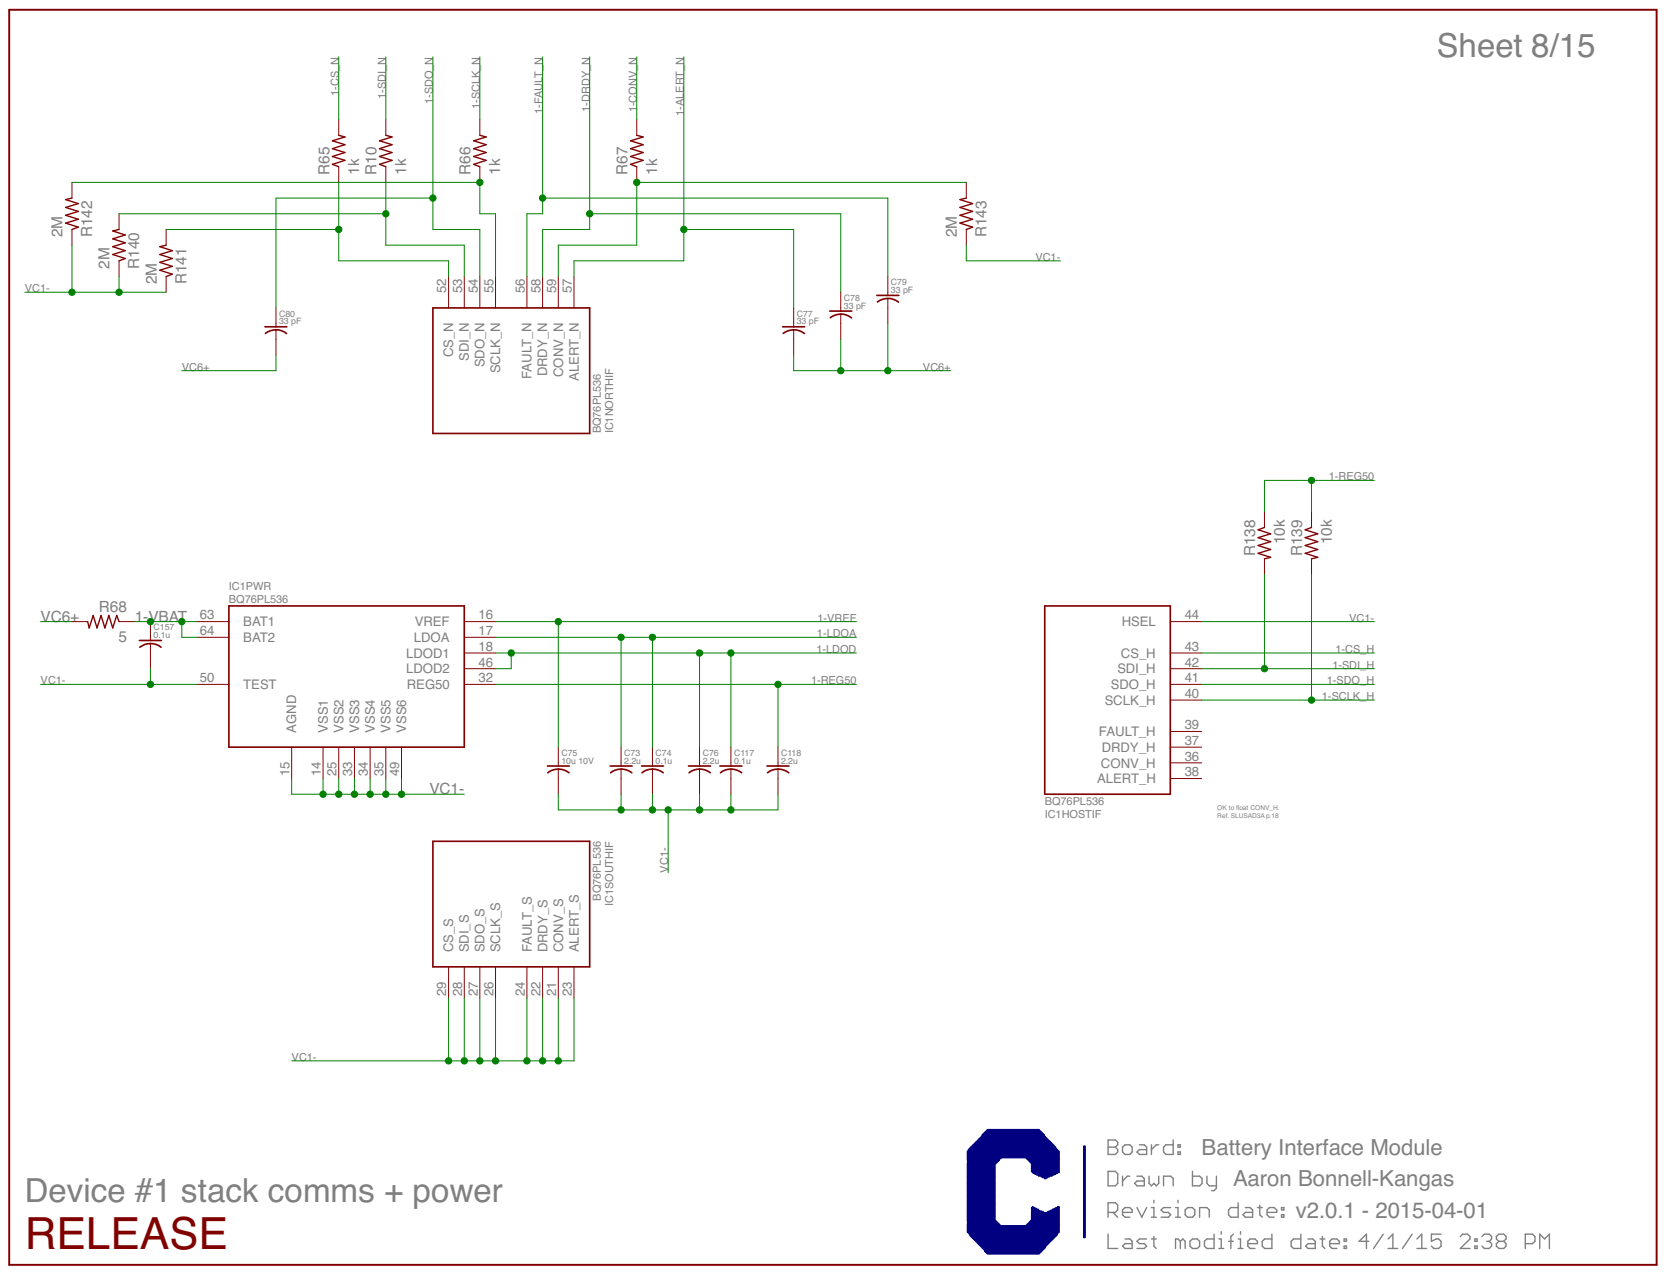
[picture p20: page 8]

OK to float CONV_H. Ref. SLUSAD3A p.18

Device #1 stack comms + power

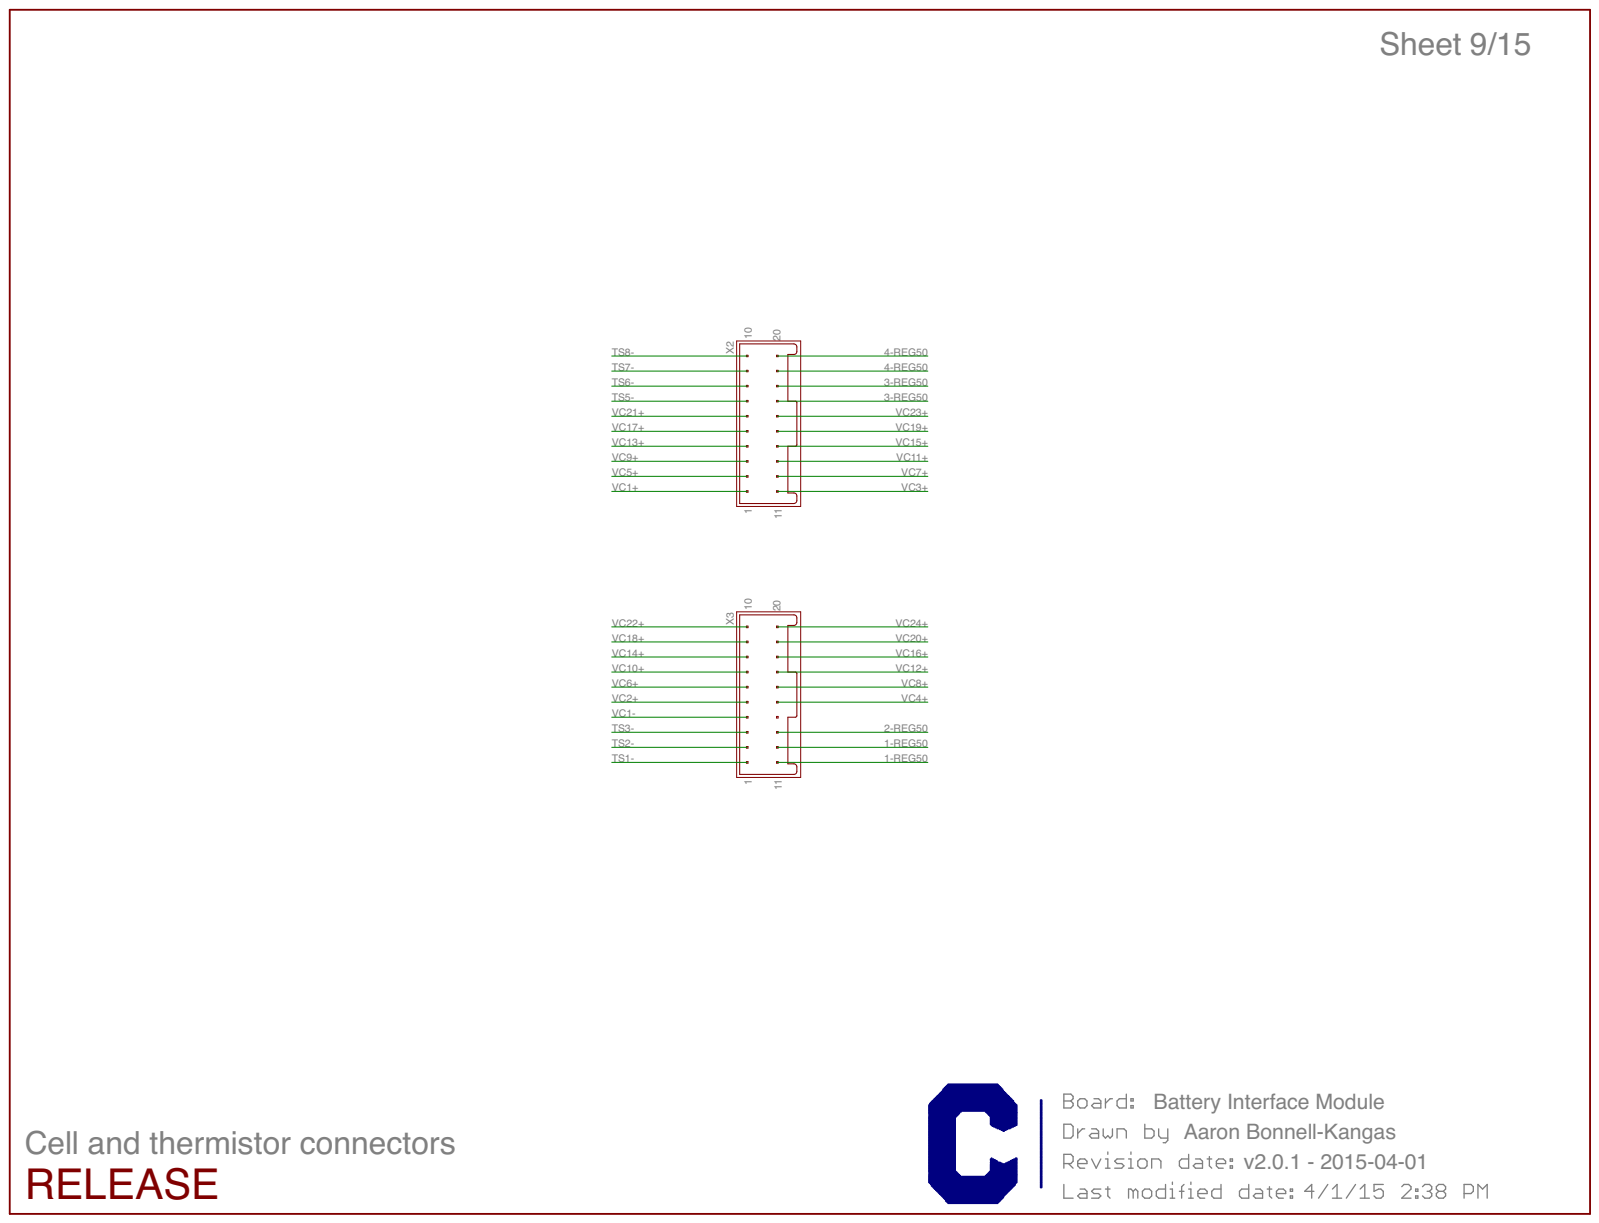
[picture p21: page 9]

v2.0.1 - 2015-04-01 Cell and thermistor connectors

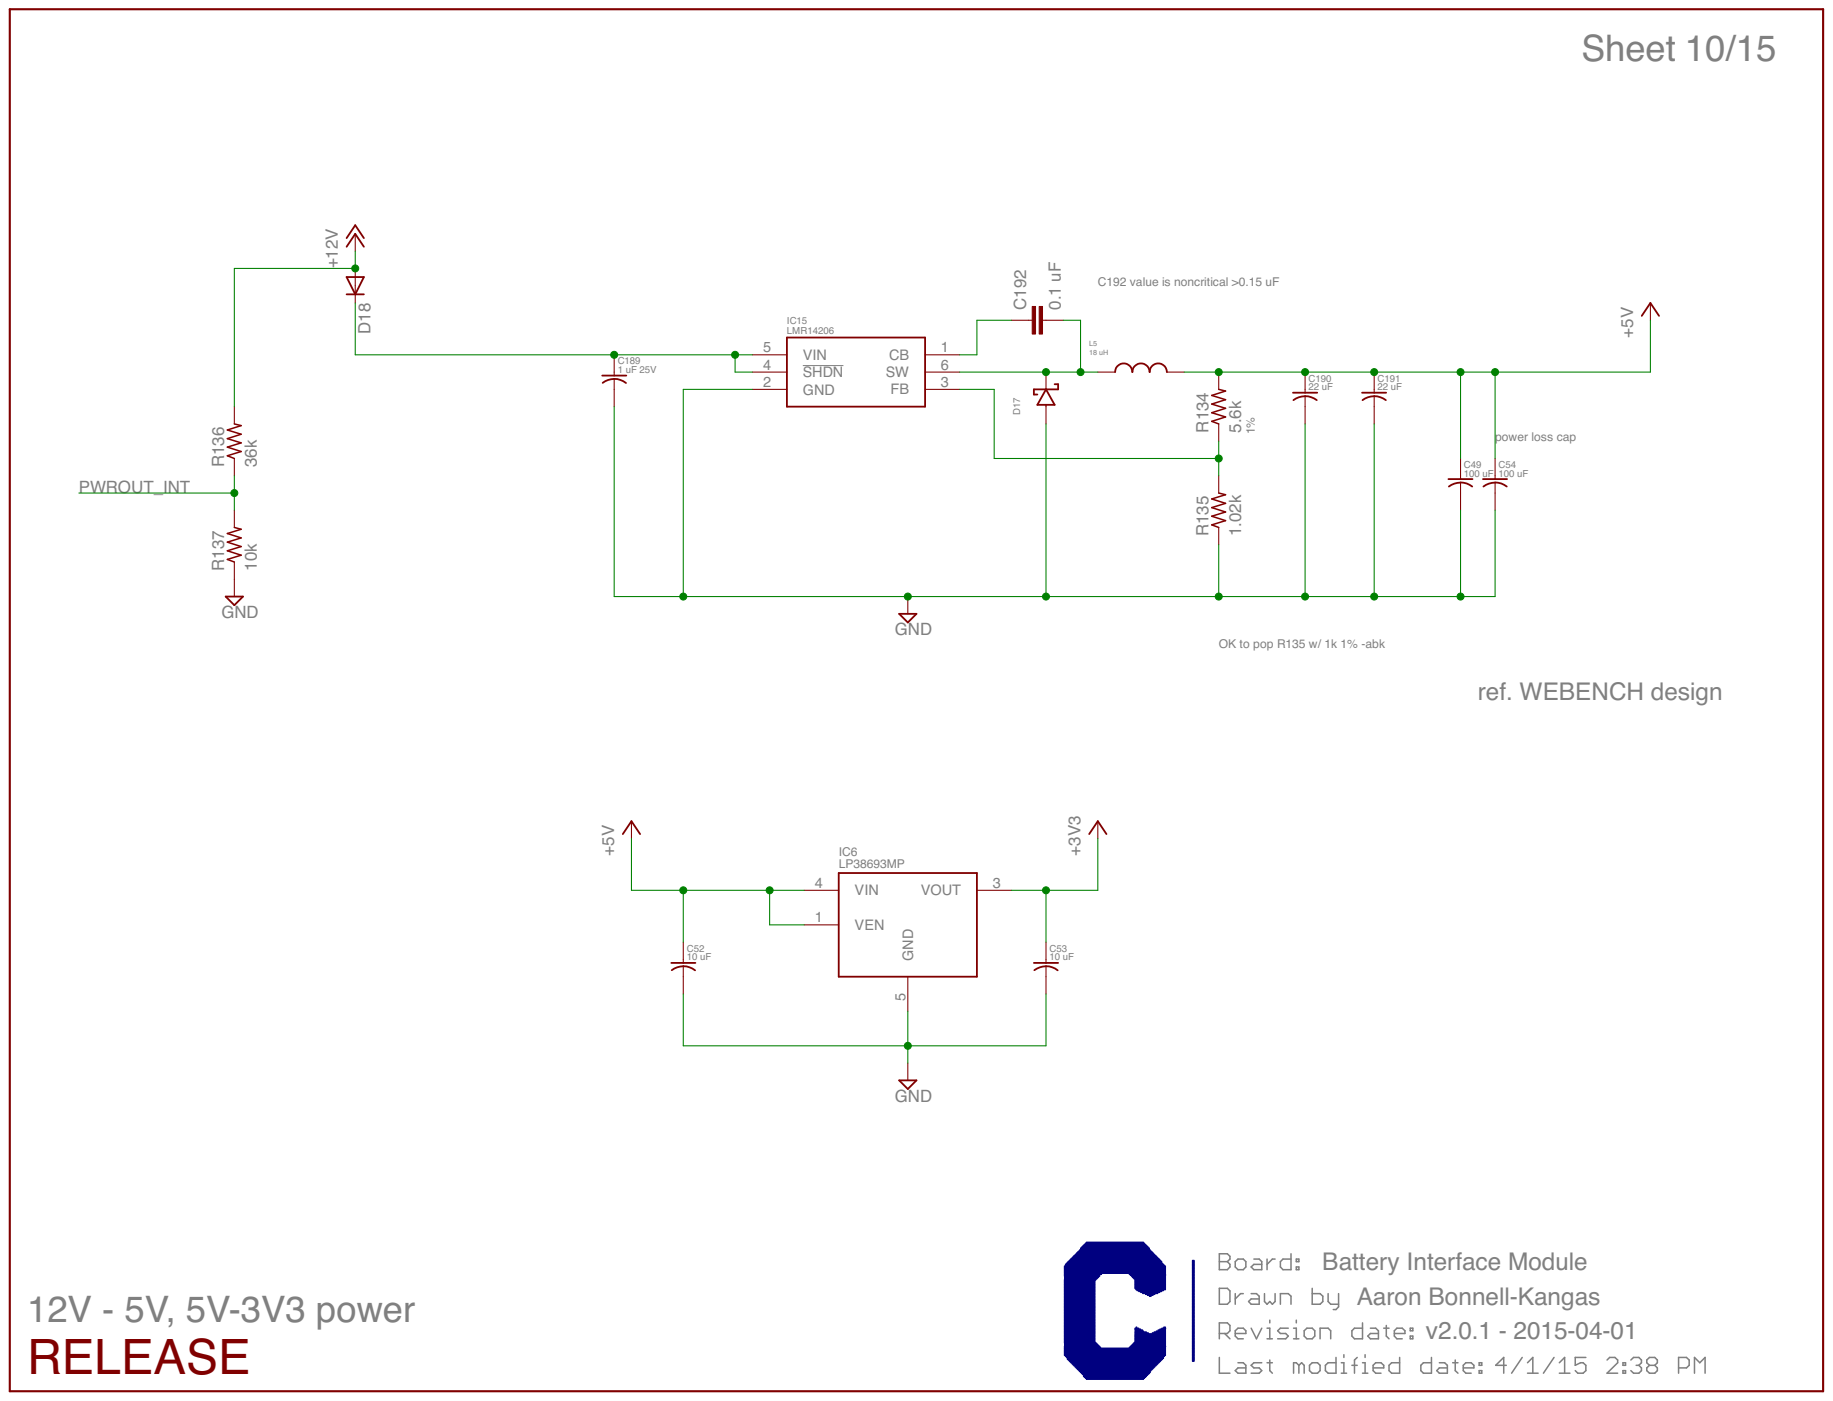
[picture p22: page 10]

C192 value is noncritical >0.15 uF

OK to pop R135 w/ 1k 1% -abk

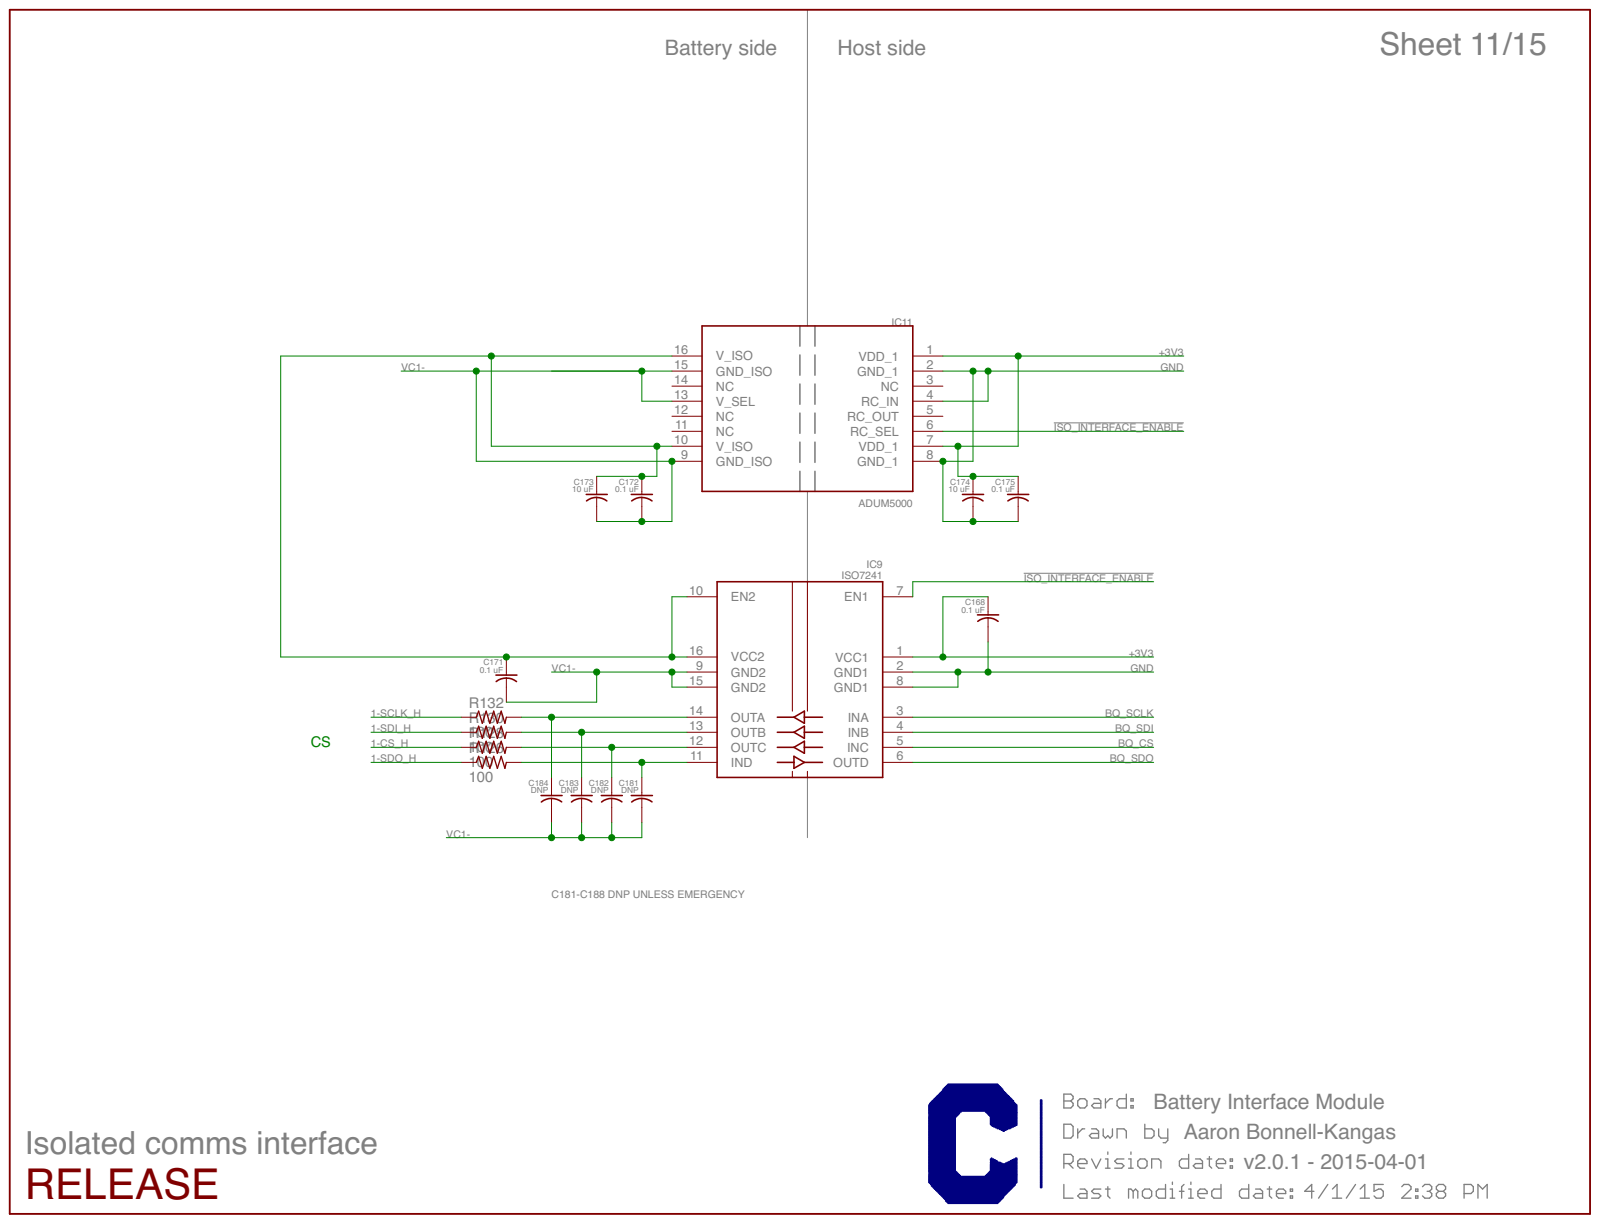
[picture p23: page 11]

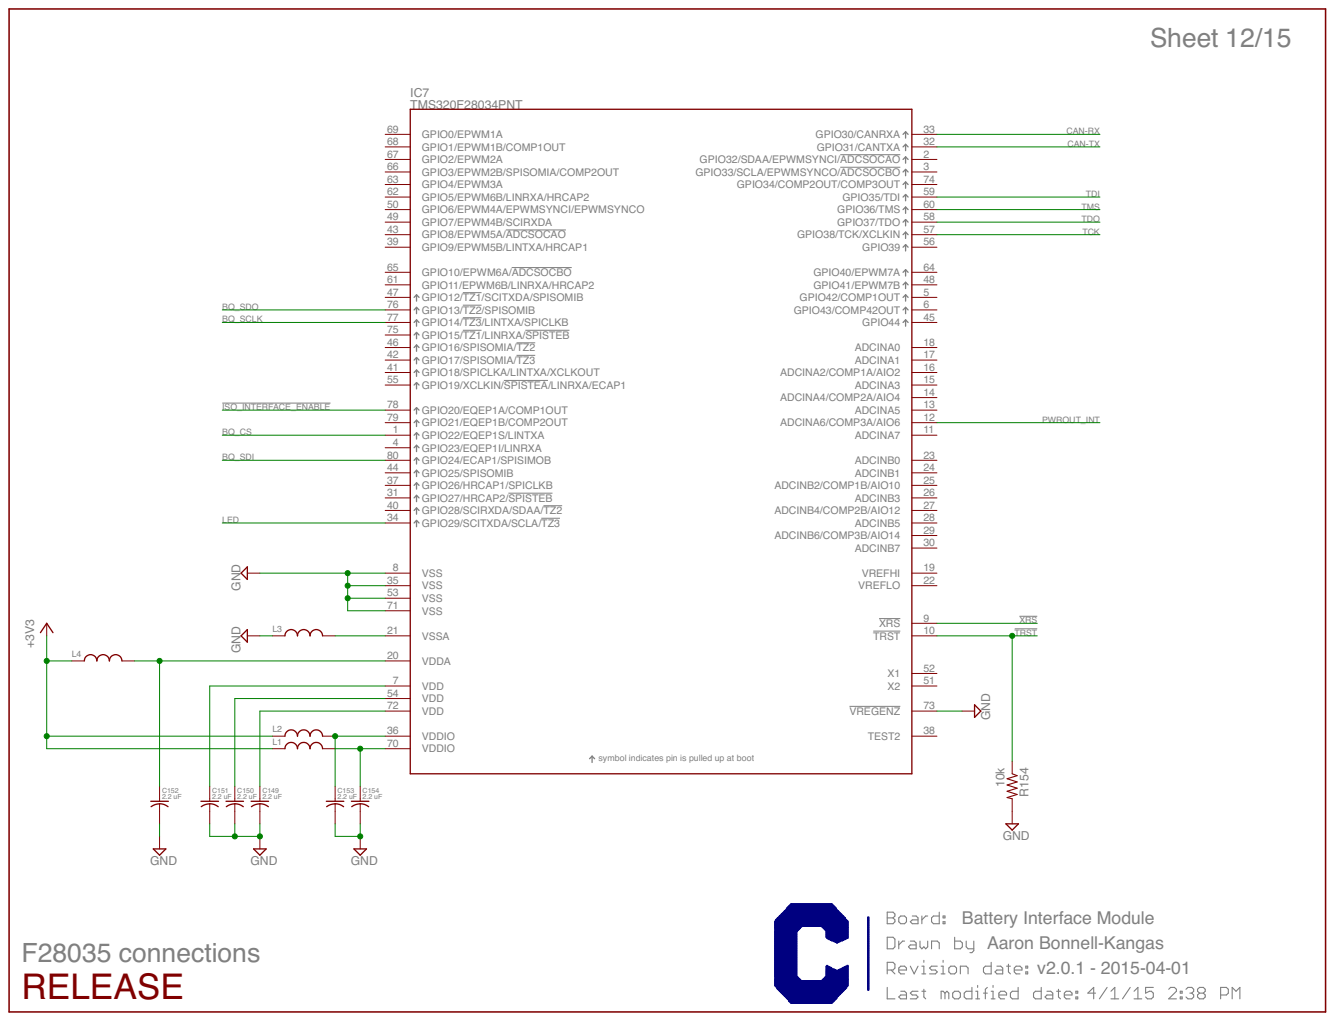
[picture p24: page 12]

CAN-RX CAN-TX

symbol indicates pin is pulled up at boot


THIS MIGHT BE THE WRONG SWITCH RELEASE

CAN interface and termination


pogo pin conn - use Panduit CBP25-C for fastening











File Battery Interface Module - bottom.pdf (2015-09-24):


Fp 33 Fp 33 Fp 33 Fp 33 33 pF 33 pF 33 pF 33 pF 33 pF 33 pF 33 pF 33 pF Fp 33 Fp 33 Fp 33 Fp 33 33 pF 33 pF 33 pF 33 pF V01 u01 33 pF 33 pF 33 pF 33 pF 1.82k 1.47k Fu 2. 2 2.2 uF2.2 uF 2.2 uFFu 2. 2 Fu 2. 2 ADUM5000 1.47k 1.82k 1.47k 1.82k 1.47k74. 1 k 1.82k 1.47k 1.82k 1.47k k74. 1 1.82k 1.47k k74. 1 0.1 uF 10 uF10 uF 0.1 uF SN74LVCG207DBV 82? 82? PND PND PND PND 60241 R ML 5.6k 1.02k V52 Fu 122 uF 22 uF 0.1 uF k63 k01 10k 10k 2M2M2M2M 510k 510k k015 k015 510k 510k k01 k01 10k k01 10k 1k1k1k1k1k1k k1k1k1k1k1k1k1k1k1k1k1k1 1k1k1k1k1k1k 0.1 uF Fn 7. 4 60 60 k1k1k1k1 k1k1k1k1 5 1. V 5 1. V 5 1. V 5 1. V 5 1. V 5 1. V V1. 5 V1. 5 V1. 5 V1. 5 V1. 5 V1. 5 V1. 5 V1. 5 V1. 5 V1. 5 V1. 5 V1. 5 5 1. V 5 1. V 5 1. V 5 1. V 5 1. V 5 1. V 0501 DVH56 NS V3 k1 98 C 09 C 19 C 29 C C85 C86 C87 C88 C105 C106 C107 C108 18 C 28 C 38 C 48 C C101 C102 C103 C104 121 C C77 C78 C79 C80 R6 R7 941 C C150C151 C152351 C 451 C1L 2L 3L L4 IC9 IC11 Q37 R15 R39 R40 R41 R4293 Q 08 R R81 R82 R83 R84 04 Q 58 R R86 R87 Q41 09 R C172 C173C174 C175 IC14 R116 R117 181 C 281 C 381 C 481 C 51 CI R134 R135 D17 981 C C190 C191 C192 81 D 631 R 731 R R138 R139 R144 R145 641 R 741 R R148 R149 451 R 551 R R157 851 R R161 R5 R4 R14 R16 R17 R18 3 R02 R 12 R 22 R 32 R 42 R2 R62 R 72 R 82 R 92 R 03 R R1 R32 R3 R34 R35 R36 D1 D2 C50 15 C R38 R43 74 R 84 R 94 R 05 R 56 R 01 R 66 R 76 R D3D4D5D6D7D8 9D 01D 11D 21D 31D 41D 51D 61D 91D 02D 12D 22D D23 D24 D25 D26 D27 D28 92D 31 R






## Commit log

2014-05-25 Bring into source control
    [BIM r02 BOM 2014-02-10.csv, Battery Interface Module.brd, Battery Interface Module.sch]
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2014-10-26 Draft board layout for 18650-compatible 24s module with revised connectors.
    [Battery Interface Module.brd, Battery Interface Module.sch]
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2014-11-05 Kim added stuff like capacitors and resistors
    [BIM power supply.sch]
2014-11-17 Copied circuit for four sheets and put down a bim connector
    [BIM power supply.sch]
2014-11-23 Kim completed BIM power supply board with additional components (connectors, fuses, potentiometers), traces, and labels
    [BIM power supply.brd, BIM power supply.sch]
2014-11-24 Edited partsdb for bom
    [BIM power supply.brd, BIM power supply.sch]
2014-11-24 Add mechanical mockups of 24s BIM
    [2014-10-26 BIM mockup.SLDDRW, 2014-10-26 BIM mockup.SLDPRT]
2014-11-27 Draft layout of new orientation to fit in RW-3 pack
    [Battery Interface Module.brd, Battery Interface Module.sch]
2014-12-15 This version passes ERC
    [BIM power supply.brd, BIM power supply.sch]
2014-12-15 This version passes DRC
    [BIM power supply.brd, BIM power supply.sch]
2014-12-15 Fixed printing error
    [BIM power supply.brd]
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2015-01-14 Switch to 2x18pos connectors (top and bottom shelf)
    [Battery Interface Module.brd, Battery Interface Module.sch]
2015-01-14 Add new CAN circuit, hook up thermistors, add CAN termination
    [Battery Interface Module.brd, Battery Interface Module.sch]
2015-01-22 Attempted redesign to squash height
    [Battery Interface Module.brd, Battery Interface Module.sch]
2015-01-22 Revise CAN ckt to use SN65HVD1050
    [Battery Interface Module.brd, Battery Interface Module.sch]
2015-01-22 change from large alum elec power loss cap (1000 uF) to 2x 100 uF tantalum caps to save space and because I hated soldering that thing
    [Battery Interface Module.brd, Battery Interface Module.sch]
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2015-02-03 Increase vertical symmetry by 35%
    [Battery Interface Module.brd]
2015-02-06 Update per-cell pi filter: terminate capacitors at n-VSS instead of VC(n-1) - per TI recommendation
    [Battery Interface Module.brd, Battery Interface Module.sch]
2015-02-18 Beginning of cell voltage routing and cell filter layout
    [Battery Interface Module.brd, Battery Interface Module.sch]
2015-02-19 Cell routing; thermistor ckt placement
    [Battery Interface Module.brd, Battery Interface Module.sch]
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2015-02-20 Add series resistance to VBAT lines
    [Battery Interface Module.brd, Battery Interface Module.sch]
2015-02-24 route so hard mfrs wanna follow-me?
    [Battery Interface Module.brd, Battery Interface Module.sch]
2015-02-24 bottom half of HV side pretty much routed
    [Battery Interface Module.brd]
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2015-02-26 To double check, I recreated the gerbers and double checked the bom. BOM is correct.
    [BIM power supply_BOM.csv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]
2015-02-28 Add MCAD files for BIM and BIM cover
    [90116A020.SLDPRT, BIM PCB.SLDPRT, BIM.SLDASM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]
2015-02-28 Add notes on changes needing to be made for mechanical integration
    [Battery Interface Module.brd]
2015-03-01 Route n-VSS signals on devices 1 and 2
    [Battery Interface Module.brd, Battery Interface Module.sch]
2015-03-01 routing work on lv gnd
    [Battery Interface Module.brd, Battery Interface Module.sch]
2015-03-01 Add part numbers to components
    [Battery Interface Module.sch]
2015-03-02 Board mostly routed, needs DRC fixes
    [Battery Interface Module.brd, Battery Interface Module.sch]
2015-03-13 Add mounting tabs to BIM PCB.
    [BIM PCB.SLDPRT, BIM.SLDASM]
2015-03-13 Remove old files from v1.01 (r02).
    [2014-10-26 BIM mockup.SLDDRW, 2014-10-26 BIM mockup.SLDPRT, BIM r02 BOM 2014-02-10.csv]
2015-03-13 Update top board drawing pdf. Clean up junk from .brd file.
    [Battery Interface Module.brd, Battery Interface Module.sch]
2015-03-14 create "BIM Mount" as example of mounting requirements for BIM
    [BIM mount.SLDPRT, BIM.SLDASM]
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2015-03-15 Add "BIM mount" component - recommended mounting interface
    [BIM mount.SLDPRT, BIM.SLDASM]
2015-03-15 Draft mech. drawing of mechanical interface
    [BIM.SLDDRW]
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2015-03-17 Fix error from SN65HVD1050 package update. Connect onboard thermistor R114.
    [Battery Interface Module.brd, Battery Interface Module.sch]
2015-03-18 Correct ERC/DRC errors.
    [Battery Interface Module.brd, Battery Interface Module.sch]
2015-03-18 Add test points for common signals. Resolve DRC/ERC errors.
    [Battery Interface Module.brd, Battery Interface Module.sch]
2015-03-23 Add more silk labels. Clean up ERC/DRC. Fix title blocks.
    [Battery Interface Module.brd, Battery Interface Module.sch]
2015-03-25 Add silkscreen indicators to some components to indicate placement orientation.
    [Battery Interface Module.brd, Battery Interface Module.sch]
2015-03-25 Fix some labels being on the wrong layer. Ignore CAM junk.
    [Battery Interface Module.brd]
2015-03-25 Shift some traces around to avoid keepout area under screw heads.
    [Battery Interface Module.brd]
2015-03-26 Update board with library changes. Update C192 value to match production usage. More rerouting.
    [Battery Interface Module.brd, Battery Interface Module.sch]
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2015-03-27 Remove mounting tabs from LV side of board.
    [Battery Interface Module.brd, Battery Interface Module.sch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]
2015-03-27 Add "DANGER: HIGH VOLTAGE" warning text and symbol on bottom side of board.
    [Battery Interface Module.brd, Battery Interface Module.sch]
2015-03-30 Regenerate Gerbers for paranoia. Update version numbers for v2.0.0 release.
    [Battery Interface Module.brd, Battery Interface Module.sch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]
2015-04-01 Increase label size for test points. Bump to v2.0.1.
    [Battery Interface Module.brd, Battery Interface Module.sch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]
2015-04-03 Change VC1 filter capacitors to 1 uF per datasheet recommendation (#4)
    [Battery Interface Module.brd, Battery Interface Module.sch]
2015-04-04 Update solder paste layer on .brd with library changes
    [Battery Interface Module.brd, Battery Interface Module.sch]
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2015-04-15 Add HV symbol. Route traces. Add labels. Tweak board outline.
    [Battery Interface Module.brd, Battery Interface Module.sch]
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
